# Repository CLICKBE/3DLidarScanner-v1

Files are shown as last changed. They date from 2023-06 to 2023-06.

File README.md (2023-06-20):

# 3D LiDAR scanner v1 - With Adafruit Mini Pan-Tilt and ESP32-C3-DevKitM

This repository demonstrates a homemade 3D LiDAR scanner made out of a [Benewake TF-Mini](https://www.gotronic.fr/art-capteur-de-distance-lidar-tf-mini-27615.htm) LiDAR sensor and [Adafruit Mini Pan-Tilt Kit](https://www.adafruit.com/product/1967). This scanner can produce 3D cloud points of spaces and was made to extract 3D point clouds of objects by subtracting two scans : one of the background and one of the object in the space. The two steps (scan of the background and scan of the background  and the object) can be triggered with a physical button. Once the object cloudpoint is extracted, we planned to determine its height and gravity center 3D position to place it in the center of the space (not yet implemented).

|scannerLidar-stepper | scan3D-exemple|
| :---: | :---: |
| The 3D LiDAR scanner | Example of 3D visualisation of the scanning |

## Files in the repository
- src/* : All the files use to run the program;
- 3D_support: folder containing the 3D model for TFMini holder to be placed on the Adafruit pantilt;
- fritzing: [Fritzing](https://fritzing.org/) file used to draw the connections picture.

## Using the 3D LiDAR scanner v1 - With Adafruit Mini Pan-Tilt

### Code

This code has been developed with VSCode and PlatformIO backend. This repo therefore reproduced the folder structure used in such project. Once you opened VSCode, open PlatformIO home page and hit Open Project button. Then, select the folder of the repository.

If you don't know anything about VSCode and PlatformIO, here's a link to set you up: [https://platformio.org/install/ide?install=vscode](https://platformio.org/install/ide?install=vscode).

### Parts
See `3DLiDAR_scanner-v1-BOM.csv`at the root of this repository.

Power is handled by an external power supply delivering 9V, 1.5A. 

### Connection

3DLidarScanner-v1

### Library needed : 
- TFMPlus: [https://github.com/budryerson/TFMini-Plus](https://github.com/budryerson/TFMini-Plus), no licence so author's right. 
- ESP32Servo: [https://github.com/madhephaestus/ESP32Servo](https://github.com/madhephaestus/ESP32Servo), GPL2.1 

Those libraries are not included in this git repository but are referenced in the platformio.ini file and therefore should directly be downloaded by PlatformIO extension of VSCode when building the code. As none of those libraries are made available with persmissive open-source licence type, you have to contact the libraries authors if you want to include them in a product. 

## 3D Visualization :
To perform a quick 3D visualization based on the serial data you can use the Processing script developed by Dana Peters : [LidarScanner.pde](https://drive.google.com/file/d/1D5wfzA8i0Pzh4qe-1skmpnqmhrvaq9d3/view?usp=drive_web) who also developed a [3D LiDAR scanner](https://www.qcontinuum.org/lidar-scanner).

In order to use this script, you will need free [Processing](https://processing.org/) software.

In order to send commands from this Processing sketch to the scanner, you can modified the `keyPressed()` function of the code by adding the following `else` condition to the `if, else if` statements that are present :  
```java
else 
{
    try 
    {
      serial.write( key );
      println( "Sending command to scanner" );
    }
    catch (Exception e)
    {
      println( "Exception " + e );
    }
}
```

## License
 © 2022 – CLICK - Université de Mons

3D LiDAR scanner with stepper motors – CLICK - UMONS (Loïc Reboursière) is free software: you can redistribute it and/or modify it under the terms of the Apache License Version 2.0. This program is distributed in the hope that it will be useful, but WITHOUT ANY WARRANTY; without even the implied warranty of MERCHANTABILITY or FITNESS FOR A PARTICULAR PURPOSE.  See the Apache License Version 2.0 for more details.
You should have received a copy of the Apache License Version 2.0 along with this program.  If not, see http://www.apache.org/licenses/
Each use of this software must be attributed to University of MONS – CLICK (Loïc Reboursière).
Any other additional authorizations may be asked to avre@umons.ac.be.

## Legal Notices
This work was produced as part of the FEDER Digistorm project, co-financed by the European Union and the Wallonia Region.

Logo FEDER-FSE

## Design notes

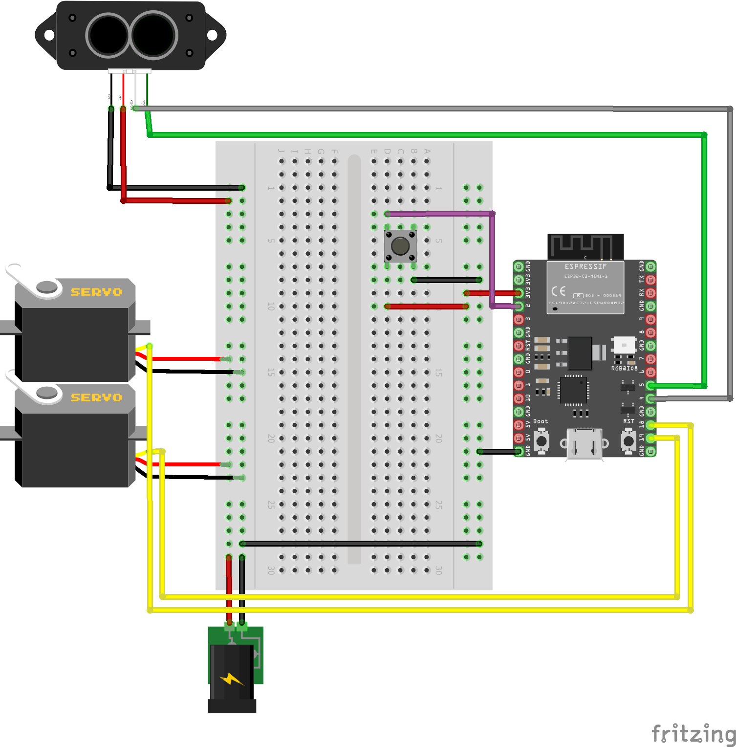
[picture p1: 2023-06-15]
fritzing/3DLidarScanner-v1.png

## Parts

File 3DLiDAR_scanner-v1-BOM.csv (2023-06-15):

Reference | Type | Quantity | Manufacturer | Link | Info
ESP32-C3-DevkitM | Microcontroller | 1 | Espressif Systems | https://www.gotronic.fr/art-carte-esp32-c3-devkitm-1-34172.htm
Mini-PanTilt Kit | Pan/tilt arm | 1 | Adafruit | https://www.adafruit.com/product/1967
SG90-SG92 | Micro-servomotor | 2 | Tower Pro | https://www.adafruit.com/product/169 | not to buy, included in Adafruit Mini Pan-Tilt Kit
COM-00097 | Push Button | 1 | Sparkfun | https://www.mouser.fr/ProductDetail/SparkFun/COM-00097?qs=WyAARYrbSnbn3fwRSgKrFQ%3D%3D
TF-Mini-S | LiDAR | 1 | Beneware | https://www.gotronic.fr/art-capteur-de-distance-lidar-tf-mini-27615.htm

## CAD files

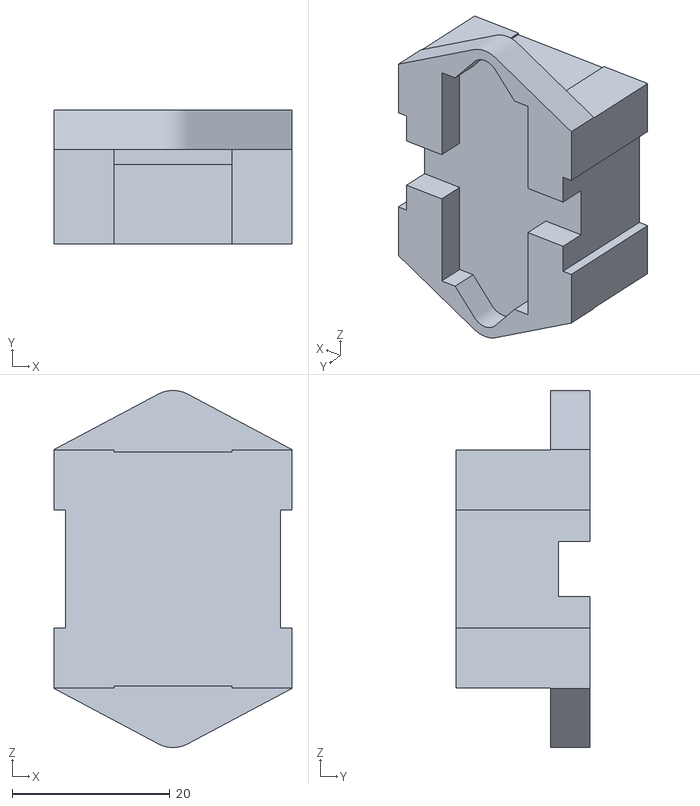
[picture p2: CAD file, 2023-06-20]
3D_support/support_lidar_v4.stl
30.1 x 17.0 x 45.2

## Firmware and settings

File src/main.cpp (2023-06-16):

/**
 * 
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
 * @copyright Copyright (c) 2023
 * 
 */



//-----------------------------------------------
// 3D LiDAR scanner based on ESP32-C3-DevKitM1
//------------------------------------------------
// Elements :
// * TFMini-S
// * Adafruit pantilt with 2 Tower Pro sg90 servo motors
// * ESP32-C3-Devkit-M1
// * External power plug (5V, 2A) with positive center
// Lib : 
// * Fork of ESP32Servo : https://github.com/loicreboursiere/ESP32Servo || LGPL  
// * TFMini-Plus library (compatible TFMini-S): https://github.com/budryerson/TFMini-Plus || None
// * https://github.com/me-no-dev/ESPAsyncWebServer || LGPL
//    * Modifications
//      * in AsyncWebSocket.cpp, replace return IPAddress(0U) by IPAddress((uint32_t)0) 
//          >> SRC : https://github.com/me-no-dev/ESPAsyncWebServer/issues/1101
//      * in WebAuthentification.cpp, replace mbedtls_md5_starts(&_ctx) by mbedtls_md5_starts_ret(&_ctx)
//            >> SRC : https://github.com/me-no-dev/ESPAsyncWebServer/issues/1147
//
//
// Connections : 
// * TFMini-Plus RX (white) >> 5
// * TFMini-Plus RX (green) >> 4
// * TFMini-Plus + >> + external Power Plug
// * TFMini-Plus GND >> GND ESP32-C3-Devkit-M1
// * horizServoPin >> 19
// * vertServoPin >> 18
// * horizServo + >> + external power plug
// * horizServo GND >> GND external power plug
// * vertServo + >> + external power plug
// * vertServo GND >> GND external power plug
// * GND ESP32-C3-Devkit-M1 >> GND external power plug
// Sources : 
// * https://how2electronics.com/how-to-use-tfmini-s-lidar-distance-sensor-with-arduino/
// * https://github.com/TravisLedo/LidarScanRender
// Author :
// * loic.reboursiere@umons.ac.be  

// TODO : 
// 16/12/2022 : Check if SIGNAL WEAK LiDAR message means distance = 0 

#include <Arduino.h>

#ifdef ESP32
#include <ESP32Servo.h>
//#include <SPIFFS.h>
//#include "ESPAsyncWebServer.h"
//const char *renderer = 
//#include "Renderer.h"
#else
#include <Servo.h>
#endif

#include <TFMPlus.h>
//#include <WiFi.h>
//s#include "stdio.h"
//#include "time.h"

#include "variables.h"
#include "computations.h"
#include "scanner.h"
#include "scannerServer.h"

//#define TFMINI_BAUDRATE 115200
//#define TF_SERIAL Serial1
//#define TF_RX 5
//#define TF_TX 4
#define CMD_BTN_PIN 2

#define OUTPUT_JS 0
#define OUTPUT_SERIAL 0

//USed to output prints functions to serial Monitor
#define DEBUG 1
#define VERBOSE 1

String header;

// Current time
unsigned long currentTime = millis();
// Previous time
unsigned long previousTime = 0; 
// Define timeout time in milliseconds (example: 2000ms = 2s)
const long timeoutTime = 2000;

Servo myservo_horiz; 
Servo myservo_vert;

//TFMini tfmini;
TFMPlus tfmS;// The used sensor is the TFMini-S compatible with the TFMiniPlus

int pointIdx = -1;
//HardwareSerial * TFSerComm;
String ledState;
// PINS
int led_test = 13;

#ifdef ESP32
int horizServoPin = 19;
int vertServoPin = 18;//18;
#define TIMER_WIDTH 10
#else
int horizServoPin = 8;
int vertServoPin = 9;
#endif

//float pi = 3.14159265;
//float deg2rad = pi / 180.0;

#define MAX_PROG_STEP 2 // Max nb of steps the program can go through
int nbBtnClick = 0; //Count click on the button : 1 is scan background, 2 is scan with object, 3 is send center information
int nbBtnClick_previous = 0;
unsigned long lastDebounceTime = 0;  // the last time the output pin was toggled
unsigned long debounceDelay = 50;  
int buttonState;  
int lastButtonState = LOW;

char backgroundSavePath [] = "/";
char withObjectSavePath [] = "/";

// Command from webpage
const char * PARAM_INPUT_1 = "prog_step";

// To be able to get time to write in cloudpoint file
const char* ntpServer = "pool.ntp.org";
const long  gmtOffset_sec = 0;
const int   daylightOffset_sec = 3600;


///// Matrix testing
//const int rows = 3;
//const int cols = 3;
//int bg[ rows ][ cols ]  = { { 10, 10, 10 }, { 10, 10, 10 }, { 10, 10, 10} };
//int currentImg[ rows ][ cols ] = { { 4, 5, 6 }, { 1, 2, 3 }, { 3, 7, 5} };
//int result[ rows ][ cols ];
const uint8_t rows = uint16_t( (v_stop_angle - v_start_angle) / vertServoStep );
const uint8_t cols = uint16_t( (h_stop_angle - h_start_angle) / horizServoStep );

// TODO : check how to convert rows and cols in const 
// rows = 50 & cols = 150
//uint8_t * bg = new uint8_t [ 50 ];// = new uint8_t[ rows * cols ];
//uint8_t bg [ rows ][ cols];

// CloudPoint * cloud           = new CloudPoint [ 1500 ]
// CloudPoint cloud            [ ARRAY_NB_ELEMENTS ];// = malloc(cols * rows * sizeof(CloudPoint *));//           [ 7500 ];
// CloudPoint cloudWithObject  [ ARRAY_NB_ELEMENTS ];
// CloudPoint cloudObject      [ ARRAY_NB_ELEMENTS ];

//uint16_t distances [ ARRAY_NB_ELEMENTS ];
uint16_t distances [ int( (h_stop_angle - h_start_angle)/horizServoStep * (v_stop_angle - v_start_angle)/vertServoStep ) ];

//CloudPoint * cloud [] = malloc( cols * rows * sizeof( CloudPoint ) );

void setup() {

/* Should help, in case we need malloc (Not working as is though)
  *cloud = malloc(cols * rows * sizeof(CloudPoint *));
    for (int i=0; i<(cols * rows); i++) 
    {
        //elementsInLine[i] = malloc(FILE_LINE_SIZE);
        //strcpy( elementsInLine[i], "-" ); // Filling the array with our empty character
    }
*/

  Serial.begin( 115200 );   // Intialize terminal serial port
  delay(20);               // Give port time to initalize

  Serial.println( "TFMPlus 3D Scanning" );
  printf( "%zu %zu %zu\n", sizeof(distances), sizeof(uint16_t), sizeof(distances)/sizeof(distances[0]) );
  
  scannerInit( horizServoPin, vertServoPin );//100 360

  testLidar();
  

// /*

  Serial.print( "--- Nb of values for distances array " );
  Serial.println( int( (h_stop_angle - h_start_angle)/horizServoStep * (v_stop_angle - v_start_angle)/vertServoStep ) );

  Point3D origin, aimedAtPoint;
  origin.x = origin.y = origin.z = aimedAtPoint.x = aimedAtPoint.y = aimedAtPoint.z = 0.0;
  uint16_t retrievedDistance;
  
  Serial.println( "\n///// Initiating test box boudaries");
  // TOCHECK
  scannerTestBox3Dimensions( 92, 60, 92, 180, 0, 60 );
  // OLD VERSION
  retrievedDistance = testBoxDimension( h_x_angle, v_x_angle, aimedAtPoint );
  print3DPoint( &aimedAtPoint );
  Serial.println( "----- X : retrieved distance " + String( retrievedDistance ) + " computed Distance " + String( computeDistance( origin, aimedAtPoint ) ) );
  delay( 5000 );
/*  
  retrievedDistance = testBoxDimension( h_y_angle, v_y_angle, aimedAtPoint );
  print3DPoint( &aimedAtPoint );
  Serial.println( "----- Y : retrieved distance " + String( retrievedDistance ) + " computed Distance " + String( computeDistance( origin, aimedAtPoint ) ) );
  delay( 5000 );
  retrievedDistance = testBoxDimension( h_z_angle, v_z_angle, aimedAtPoint );
  print3DPoint( &aimedAtPoint );
  Serial.println( "----- Z : retrieved distance " + String( retrievedDistance ) + " computed Distance " + String( computeDistance( origin, aimedAtPoint ) ) );
  delay( 5000 );
  Serial.println( "///// Terminating test box boudaries\n");
// */
}

//void loop() 
//{

//}

void loop() {

  if( getIsScanning() == 0 ) {
//  if( is_scanning == 0 ) {
    int reading = digitalRead( CMD_BTN_PIN );

    // check to see if you just pressed the button
    // (i.e. the input went from LOW to HIGH), and you've waited long enough
    // since the last press to ignore any noise:

    // If the switch changed, due to noise or pressing:
    if (reading != lastButtonState) {
      // reset the debouncing timer
      lastDebounceTime = millis();
    }
    
    if ( ( millis() - lastDebounceTime ) > debounceDelay ) {

      if ( reading != buttonState ) 
      {
          buttonState = reading;
          
          // only toggle next step if the new button state is HIGH
          if ( buttonState == HIGH ) {
            nbBtnClick += 1;
            //Serial.println( nbBtnClick );
            
            if( nbBtnClick == 1 ) 
            {
              //scannerTestBoxDimensions();

              Serial.println( "----- Scanning empty scene - " + String( nbBtnClick ) );
  //            is_scanning = true;
              setIsScanning( true );
              scanning( distances, false, true );
              Serial.println( "----- Scanning empty scene - DONE - is_scanning " + String( getIsScanning() ) );
              //Point3D emptyScene = computeBaseHeight( distances );
              //Serial.println( "---- Distance to limits : " + String( emptyScene.x ) + " " + String( emptyScene.y ) + " " + String( emptyScene.z ) );
              
              // getGroundDistance
              debounceDelay = 50;
              
            }
            else if( nbBtnClick == 2 ) 
            {
              Serial.println( "----- Scanning scene with objects - "  + String( nbBtnClick ) );
              //is_scanning = true;
              setIsScanning( true );
              //scanning( OUTPUT_JS, OUTPUT_SERIAL, "with_objects", withObjectSavePath, cloudWithObject, false );
              scanning( distances, true, true );
            }

            if ( nbBtnClick >= MAX_PROG_STEP ) 
            {
              nbBtnClick = 0;
            }
          }
        }

    }

    // save the reading. Next time through the loop, it'll be the lastButtonState:
    lastButtonState = reading;

  }

}

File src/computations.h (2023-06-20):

/**
 * 
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
 * @copyright Copyright (c) 2023
 * 
 */

#ifndef COMPUTATIONS_H
#define COMPUTATIONS_H

#include <Arduino.h>
#include "scanner.h"

extern  const uint8_t rows;
extern  const uint8_t cols;

/** @struct Dimension
 *  @brief This structure is used to store 3D dimensions of an object.
 *  @var Dimension::height 
 *  Height of the object.
 *  @var Dimension::width 
 *  Width of the object.
 *  @var Dimension::depth 
 *  Depth of the object.
 */
typedef struct Dimension
{
    int height;
    int width;
    int depth;
} Dimension;

/** @struct GroundsHeights
 *  @brief This structure is used to store the different "grounds" of a specific space, 
 * the actual ground of a support that can be added to the scene.
 *  @var GroundsHeights::distanceToGround 
 *  The distance from the sensor position to the actual ground.
 *  @var GroundsHeights::distanceToSupport 
 *  The distance from the sensor position to the support position.
 */
typedef struct GroundsHeights
{
    float distanceToGround  = -1.;
    float distanceToSupport = -1.;
} GroundsHeights;

/**
 * @brief Subtract two cloud points (CloudPoint []) obtained from Lidar scanner
 * 
 * @param background Cloud point of the background, without object
 * @param withObject Cloud point of the background with the object
 * @param result Cloud point representing the object aka the result of the subtraction of the withObject and background cloud points
 * @param threshold Theshold 
 */
void subtractCloudPoint( CloudPoint background[], CloudPoint withObject[], CloudPoint result[], int16_t threshold )
{
    if( sizeof( background ) == sizeof( withObject ) == sizeof( result ))
    {
        int nbElements = sizeof( *background ) / sizeof( CloudPoint );
        for( int i = 0; i < nbElements ; i++ )
        {
            if( threshold > 0 )
            {
                if( withObject[ i ].scanCoord.distance - background[ i ].scanCoord.distance < threshold )
                {
                    result[ i ].scanCoord.distance = 0;
                }
                else
                {
                    result[ i ].scanCoord.distance = 
                        withObject[ i ].scanCoord.distance - 
                        background[ i ].scanCoord.distance;
                }
            }
            else
                result[ i ].scanCoord.distance = 
                    withObject[ i ].scanCoord.distance - 
                    background[ i ].scanCoord.distance;
        }   
    }
    else
    {
        printf( "Length of arrays don't match, check number of elements" );
    }
    
}

/**
 * @fn float computeDistance ( Point3D start, Point3D stop ) 
 *
 * @brief Compute distance between two Point3D structures
 * 
 * @param start Cloud point of the background, without object
 * @param stop Cloud point of the background with the object
 * 
 * @return distanceBtwStartStop The actual distance between the two points. 
 */
float computeDistance ( Point3D start, Point3D stop ) 
{
    float distanceBtwStartStop = sqrt( pow( ( stop.x - start.x ), 2 ) 
                                     + pow( ( stop.y - start.y ), 2 ) 
                                     + pow( ( stop.z - start.z ), 2 ) 
                                    );

    return distanceBtwStartStop;
}



// TODO : algo détection sol et support
// Soit deux passes : la première pour le sol (le plus bas) la deuxième pour le support (le plsu bas après le sol)
// Soit mémoire de qq échantillons et trouver les valeurs identiques et dont les index se suivent

/**
 * @fn GroundsHeights groundAndSupportDetection2Passes( Point3D cloud [] )
 * 
 * @brief Compute the distances from the sensor to the ground and to the support object (e.g. table, box, etc.), if present, 
 * from the background cloud point variable. The cloud point is represented by an array of 3DPoint structures.
 * 
 * @param cloud Cloud point of the background, without object
 * 
 * @return heights GroundsHeights structure containing both distances 
 */
GroundsHeights groundAndSupportDetection2Passes( Point3D cloud [] )
{

    float z_max = 0, z_min = DISTANCE_MAX;
    int idx_z_max = -1;

    GroundsHeights heights;

    for( int i = 0; i < ARRAY_NB_ELEMENTS; i++ )
    {
        if( cloud[ i ].z > z_max )
        {
            z_max = cloud[ i ].z;
            idx_z_max = i;
        }
    }
    
    for( int i = 0; i < ARRAY_NB_ELEMENTS; i++ )
    {
        if( abs( heights.distanceToGround - cloud[ i ].z ) < z_min )
        {
            z_min = cloud[ i ].z;
        }
    }

    heights.distanceToGround = z_max;
    heights.distanceToSupport = z_min;

    return heights;

}

/**
 * @fn GroundsHeights computeHeights( uint16_t distances [] )
 * 
 * @brief Compute the distances from the sensor to the ground and to the support object (e.g. table, box, etc.), if present, 
 * from the background cloudpoint variable. The cloud point is represented by an array of unint16_t values.
 * 
 * @param distances Array of distances gathered from the scan of the background, without object.
 * 
 * @return heights GroundsHeights structure containing both distances. 
 */
GroundsHeights computeHeights( uint16_t distances [] )
{

    float x = 0, y = 0, z = 0;
    float z_min = DISTANCE_MAX, z_max = 0, x_min = DISTANCE_MAX, x_max = 0, y_min = DISTANCE_MAX, y_max = 0;
    int idx_z_min = -1, idx_z_max = -1, idx_x_min = -1, idx_x_max = -1, idx_y_min = -1, idx_y_max = -1;
    int height = -1;
    uint8_t h_index = -1, v_index = -1, h_angle = -1, v_angle = -1;

    Point3D distances3D;
    GroundsHeights heights;

    Serial.println( "------ Start Base computation" );


    for( int i = 0; i < ARRAY_NB_ELEMENTS ; i++ )
    {
        if ( distances[ i ] > 0 )
        {
            oneLineIndex2HorizAndVertIndex( i, &h_index, &v_index );
            pointIndexes2PointAngles( h_index, v_index, &h_angle, &v_angle ); // Still useful ?
            computeXYZ( &x, &y, &z, distances[ i ], h_angle, v_angle );

            if( z > z_max )
            {
                z_max = z;
                idx_z_max = i;
            }

        }
    }

    Serial.println( "------ Stop Base computation" );

    distances3D.x = x_max - x_min;
    distances3D.y = y_max - y_min;
    distances3D.z = z_max - z_min;

    Serial.println("x_min " + String( x_min ) + " (idx : " + String( idx_x_min ) + ")" );
    Serial.println("x_max " + String( x_max ) + " (idx : " + String( idx_x_max ) + ")" );
    Serial.println("y_min " + String( y_min ) + " (idx : " + String( idx_y_min ) + ")" );
    Serial.println("y_max " + String( y_max ) + " (idx : " + String( idx_y_max ) + ")" );
    Serial.println("z_min " + String( z_min ) + " (idx : " + String( idx_z_min ) + ")" );
    Serial.println("z_max " + String( z_max ) + " (idx : " + String( idx_z_max ) + ")" );
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
